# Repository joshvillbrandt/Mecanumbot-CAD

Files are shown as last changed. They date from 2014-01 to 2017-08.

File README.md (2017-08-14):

Mecanumbot-CAD
==============

Solidworks files for the Mecanumbot robot.

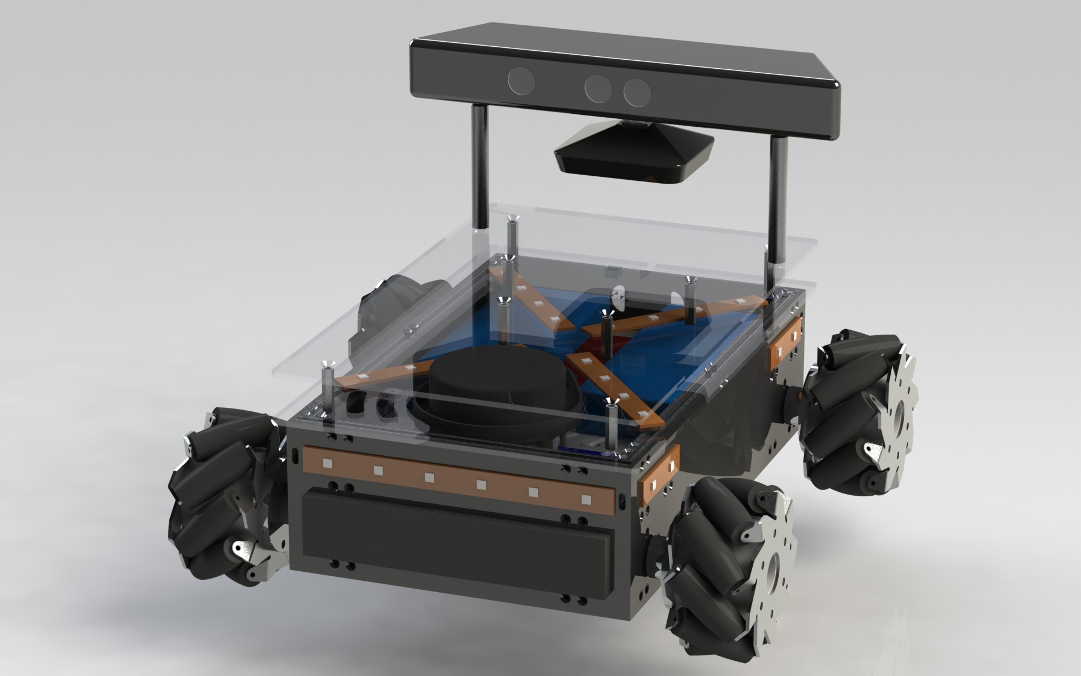
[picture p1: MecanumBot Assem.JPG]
Mecanumbot assembly screenshot


## Todo List

Problems with current design:

* very hard to service
 * too many little screws
 * the robot is very tightly packed
* placing an object on the platform blocks the view of the Kinect
* would ideally like to use a 3D sensor to identify an object on the plaform, but the Kinect's minimum distance is past the front face of the robot, so this doesn't work
* battery plugs are difficult to connect and disconnect
* current battery space was optimized for 4S lipos, but only 3s lipos are being used

Ideas for improvements

* group wires between top and bottom plates into one bundle
* would like to enable automatic charger with a charging dock
* export the model to the ROS urdf to display in rviz

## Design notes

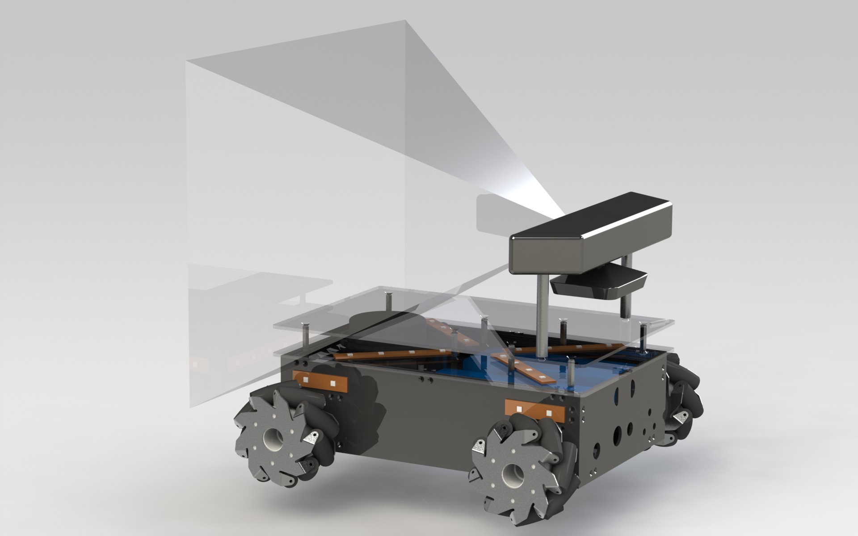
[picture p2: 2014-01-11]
MecanumBot FOV.JPG

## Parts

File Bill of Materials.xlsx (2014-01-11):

Item | Category | Quantity | Vendor | Vendor Part ID | Cost | Sub-Total | Description
12"x24"x1/8" G10/FR4 | Structure | 2 | McMaster | 85345K622 | $34.03 | $68.06
12"x24"x1/8" Polycarbonite | Structure | 3 | McMaster | 8574K41 | $12.52 | $37.56
MicroRax - Small Kit | Structure | 1 | SparkFun | PRT-10809 | $119.95 | $119.95
Devantech MD25 | Drive | 2 | RobotShop | RB-Dev-31 | $75.56 | $151.12
Devantech EMG30 | Drive | 4 | RobotShop | RB-Dev-40 | $54.66 | $218.64
Kinect | Sensor | 1 | Newegg | N82E16874103199 | $138.99 | $138.99
120W wide input DC power supply | Electronics | 1 | Mini-ITX.com | pico-PSU-120WI-25V | $55.00 | $55.00 | picoPSU-120 WI 12-25V Wide Input Plug-in DC-DC ATX PSU (192W AC Adapter Compatible)
Rosewill 1.5' USB cable | Electronics | 1 | Newegg | N82E16812119335 | $3.49 | $3.49
Zotac H67ITX-C-E Motherboard | Electronics | 1 | Newegg | N82E16813500064 | $149.99 | $149.99
PNY 8GB Memory | Electronics | 1 | Newegg | N82E16820178333 | $81.99 | $81.99
Intel Core i3-2100T 2.5GHz | Electronics | 1 | Newegg | N82E16819116394 | $134.99 | $134.99
Kingston 64GB SSD | Electronics | 1 | Newegg | N82E16820139949 | $119.99 | $119.99
Arduino Uno | Electronics | 1 | SparkFun | DEV-11224 | $29.95 | $29.95
Front bumper | Structure | 1 | McMaster | 8694K95 | $15.21 | $15.21
Silicone rubber top | Structure | 1 | McMaster | 86915K24 | $24.77 | $24.77
IDEC E-stop button | Electronics | 1 | Automation and Beyond | XA1E-BV3U01K-R | $33.00 | $33.00
PC on/off button | Electronics | 1 | Digi-Key | CKN10010-ND | $12.01 | $12.01
Power switch | Electronics | 1 | SparkFun | COM-11155 | $1.50 | $1.50
Nexus 100mm Mecanum Wheel Set | Drive | 1 | RobotShop | RB-Nex-13 | $251.66 | $251.66
Turnigy Nanotech 3S 8AHr LiPo | Electronics | 2 | Hobby King | Z80003S-30 | $46.55 | $93.10
Pressure, temp sensor | Electronics | 1 | Adafruit | 391 | $19.95 | $19.95
1m RGB LED Light Strip | Electronics | 1 | Adafruit | 306 | $29.95 | $29.95 | BMP085 breakout
Kinect Standoffs | Structure | 1 | iheartengineering | TURTLE-KINECT-STANDOFF-KIT | $14.95 | $14.95
5mm to 6mm shim | Structure | 1 | McMaster | 8751K63 | $1.20 | $1.20 | Self-lubricating Mds-filled Nylon Strip .02" Thick X 1" Wide, Black, 5 Ft. Length
microRax compatible screws | Structure | 2 | McMaster | 91294A125 | $5.00 | $10.00 | Black Alloy Steel Flat-head Socket Cap Screw, Class 10.9, M3 Size, 5mm Length, .50mm Pitch
thumb screws | Structure | 6 | McMaster | 92581A120 | $2.73 | $16.38 | Black-oxide Steel Knurled Head Thumb Screw, With Straight Shoulder, M3 Thread, 6mm Long
laser scanner | Sensor | 1 | Neato | XV-11 | $332.98 | $332.98
Neato Laser USB | Electronics | 1 | n/a | n/a | $50.00 | $50.00
Mecanumbot Power Board | Electronics | 1 | n/a | n/a | $100.00 | $100.00
xbox controller w/ play and charge | Electronics | 1 | Microsoft | B00936K09S | $61.99 | $61.99
xbox360 wireless gaming receiver | Electronics | 1 | Microsoft | B000HZFCT2 | $16.99 | $16.99
battery charger | Electronics | 1 | Hobby King |  | $22.99 | $22.99 | Turnigy Accucel-6 50W 6A Balancer/Charger w/ accessories
 |  |  |  |  |  | $2418.35

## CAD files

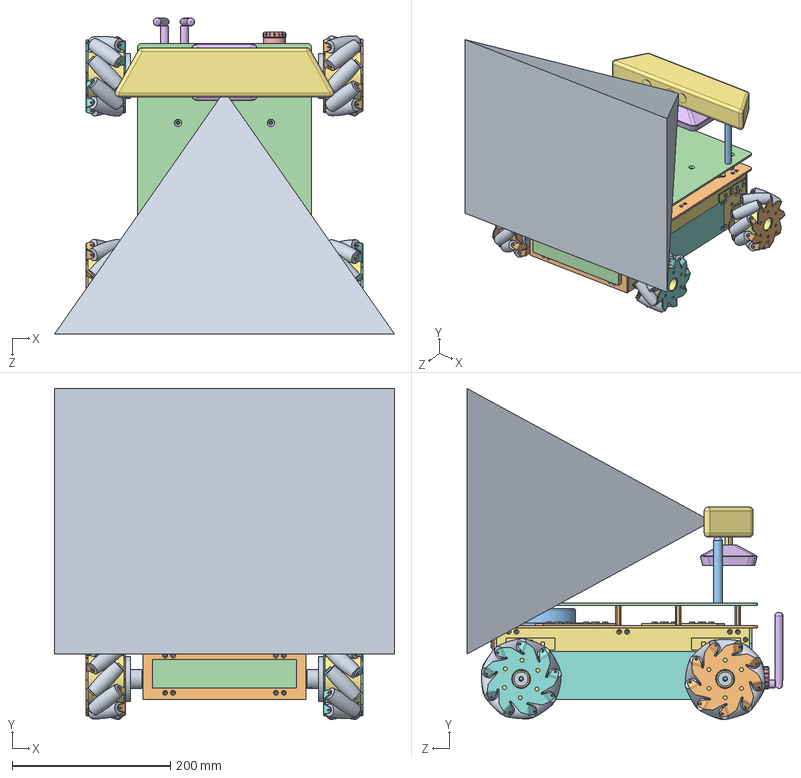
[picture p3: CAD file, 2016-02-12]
MecanumBot Assem.SLDASM
430.0 x 418.8 x 399.7 mm
Body Base Plate
MicroRAX 30cm Beam x 4
MicroRAX 20cm Beam x 4
MicroRAX 6cm Beam x 4
Zotac H67-ITX
Body Mid Plate
Body Side Plate Left
Body Side Cover x 2
Zippy 8Ah 3S1P LiPo x 2
Body Laser Plate
Neato Laser Scanner
Body Top Plate
93657A320 x 4
Kingston SSD
Arduino
Devantech MD25 x 2
MicroRAX 4cm Beam x 2
Body Front Plate
Body Back Plate
Body Back Cover
Body Side Plate Right
Microsoft Kinect Base
Microsoft Kinect Body
Devantech EMG30 x 4
Wheel Hub x 4
Power Board
93657A046 x 4
40mm Fan
93657A035 x 12
Battery Hold x 2
Adafruit 2 RGB LED Strip x 15
93657A003 x 4
95947A059 x 8
Microsoft Kinect Standoff x 2
Bumper
IDEC XA1E-BV3U01K-R
Zotac Antenna x 2
Nexus 100mm Mecanum Wheel Core x 4
Nexus 100mm Mecanum Wheel Left Plate x 4
Nexus 100mm Mecanum Wheel Roller x 36
Nexus 100mm Mecanum Wheel Right Plate x 4

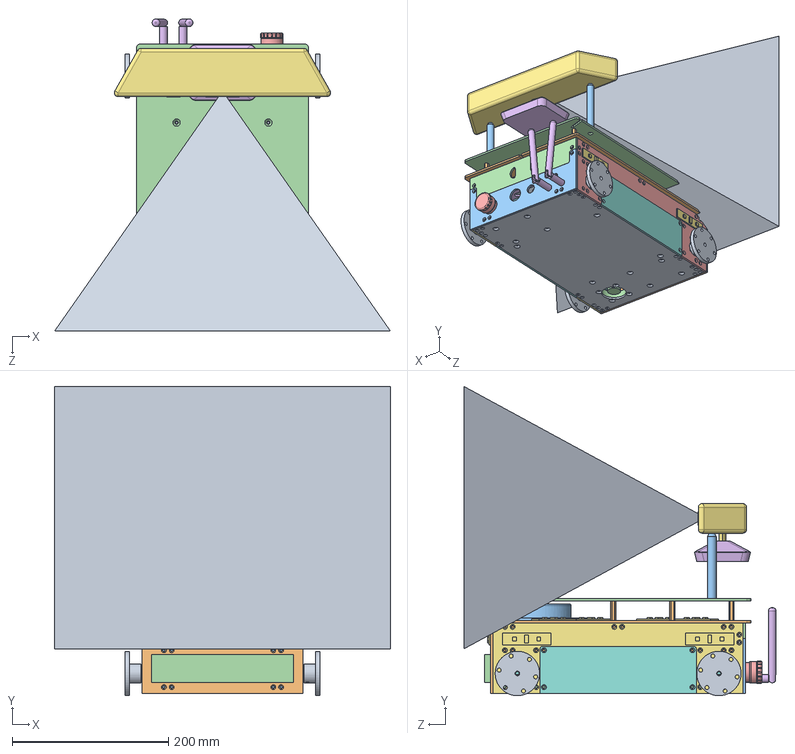
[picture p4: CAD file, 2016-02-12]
Link base_link.SLDASM
430.0 x 395.8 x 399.7 mm
Body Base Plate
MicroRAX 30cm Beam x 4
MicroRAX 20cm Beam x 4
MicroRAX 6cm Beam x 4
Zotac H67-ITX
Body Mid Plate
Body Side Plate Left
Body Side Cover x 2
Zippy 8Ah 3S1P LiPo x 2
Body Laser Plate
Neato Laser Scanner
Body Top Plate
93657A320 x 4
Kingston SSD
Arduino
Devantech MD25 x 2
MicroRAX 4cm Beam x 2
Body Front Plate
Body Back Plate
Body Back Cover
Body Side Plate Right
Microsoft Kinect Base
Microsoft Kinect Body
Devantech EMG30 x 4
Wheel Hub x 4
Power Board
93657A046 x 4
40mm Fan
93657A035 x 12
Battery Hold x 2
Adafruit 2 RGB LED Strip x 15
93657A003 x 4
95947A059 x 8
Microsoft Kinect Standoff x 2
Bumper
IDEC XA1E-BV3U01K-R
Zotac Antenna x 2

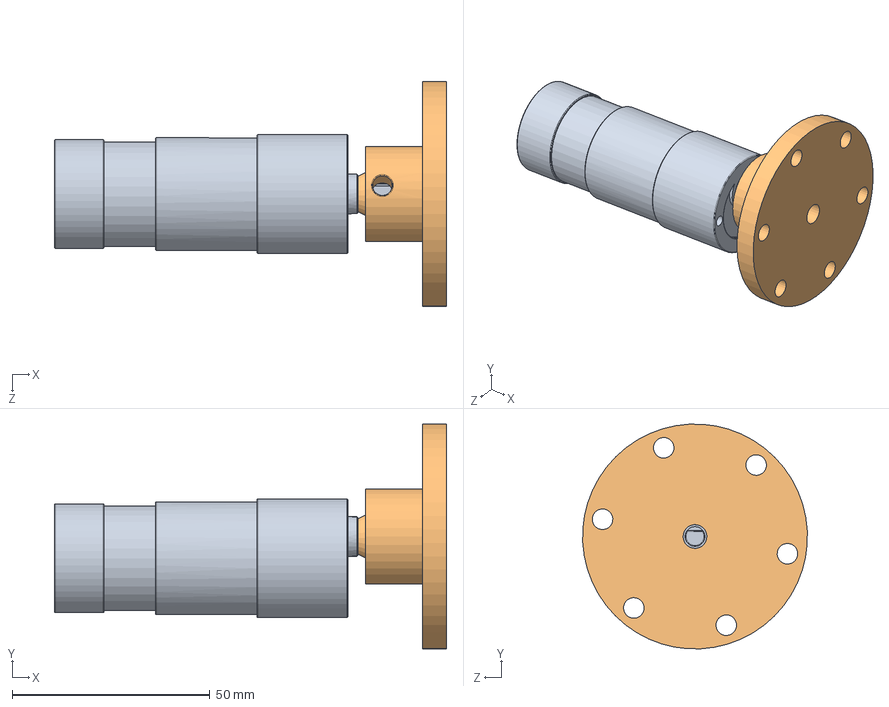
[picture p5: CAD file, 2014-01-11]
Drivetrain Left Assem.SLDASM
99.0 x 56.7 x 56.7 mm
Devantech EMG30
Wheel Hub

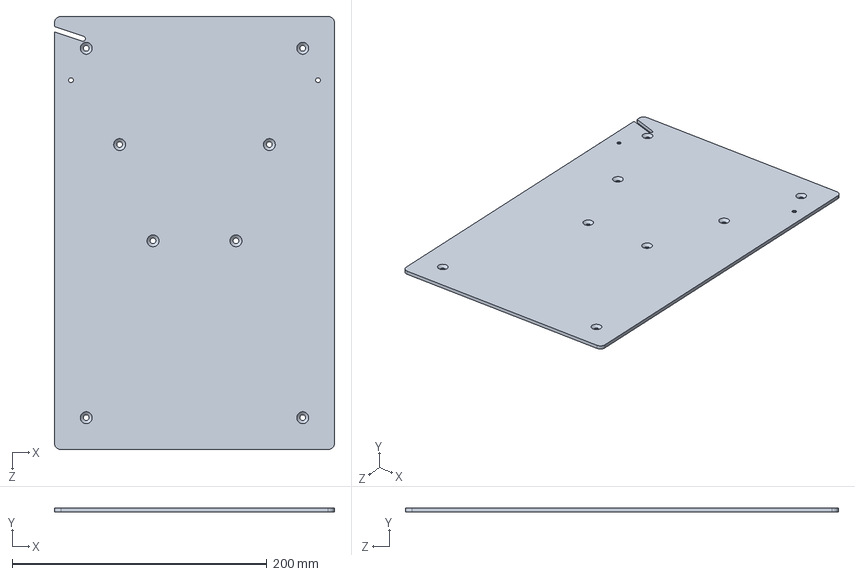
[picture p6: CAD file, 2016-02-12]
Body Top Plate.SLDPRT
220.0 x 3.17 x 340.0 mm

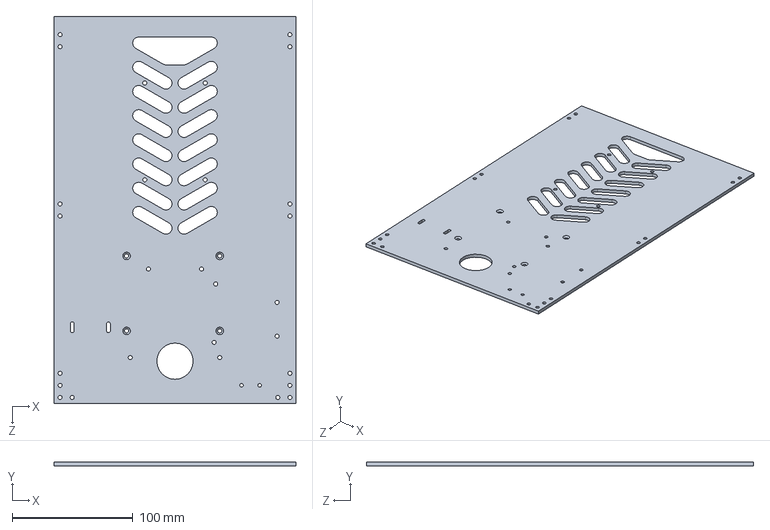
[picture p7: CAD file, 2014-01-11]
Body Mid Plate.SLDPRT
200.0 x 3.17 x 320.0 mm

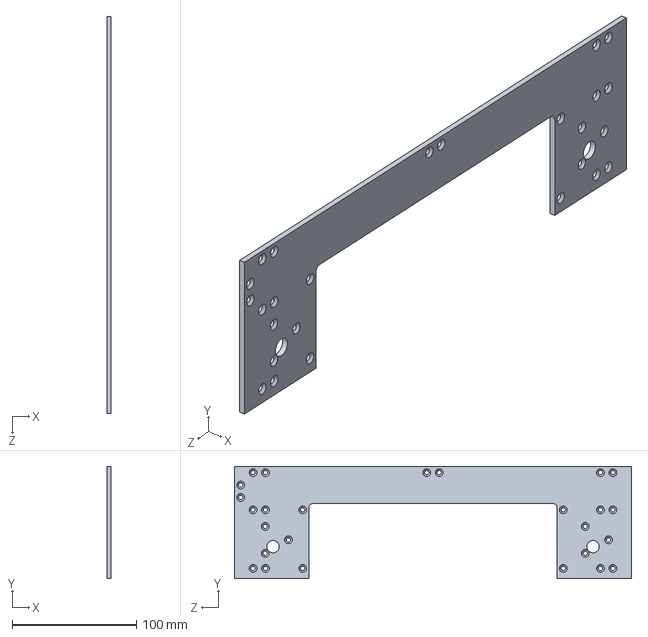
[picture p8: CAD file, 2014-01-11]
Body Side Plate Right.SLDPRT
3.17 x 90.3 x 320.0 mm

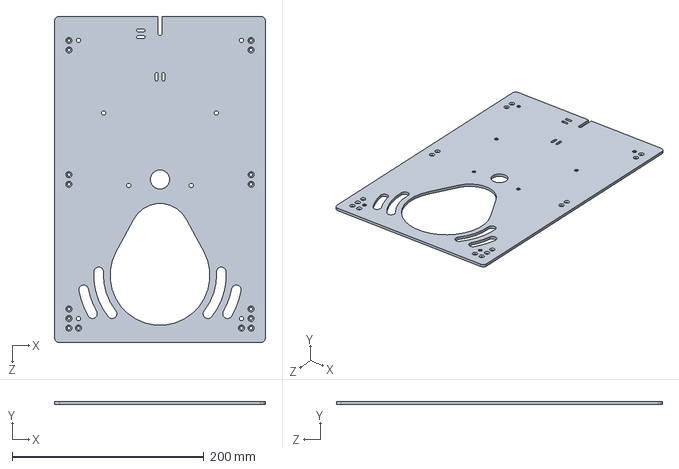
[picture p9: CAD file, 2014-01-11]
Body Laser Plate.SLDPRT
220.0 x 3.17 x 340.0 mm

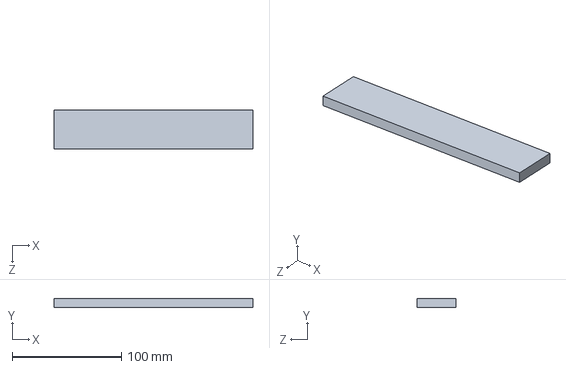
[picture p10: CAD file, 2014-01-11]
Bumper.SLDPRT
182.0 x 8.00 x 36.0 mm

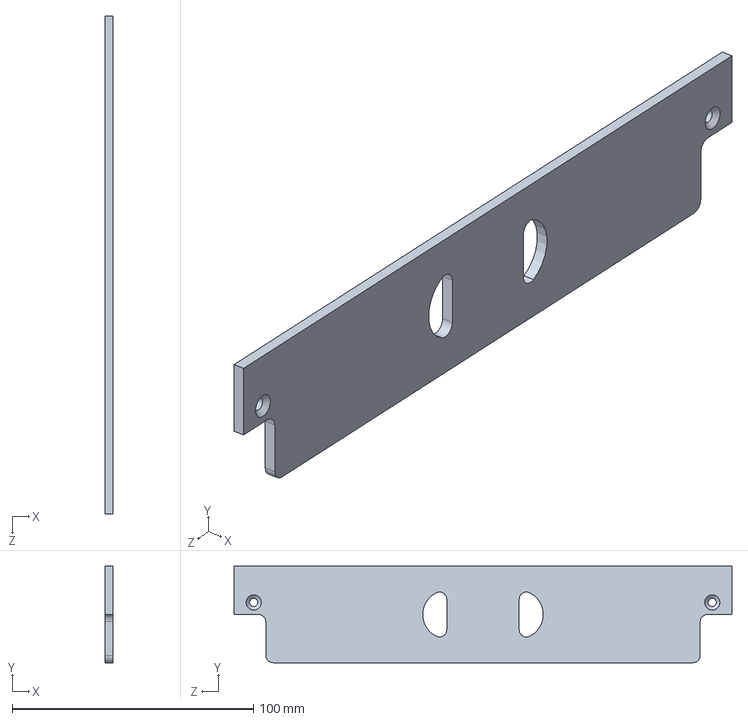
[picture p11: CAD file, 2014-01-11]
Body Back Cover.SLDPRT
3.17 x 40.0 x 206.4 mm

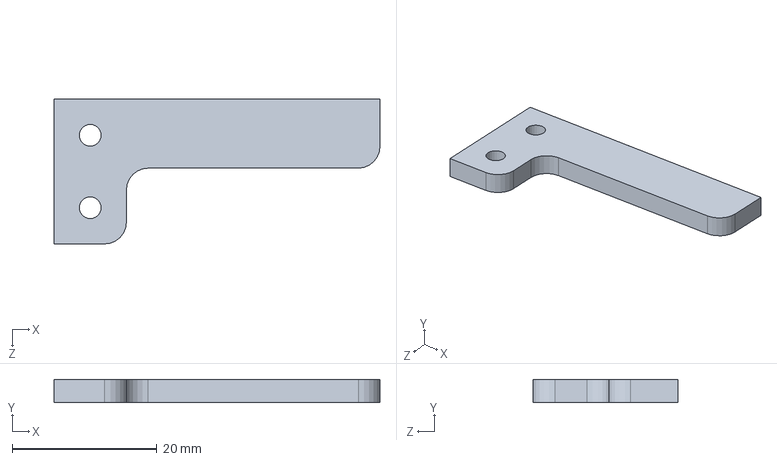
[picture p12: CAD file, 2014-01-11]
Battery Hold.SLDPRT
45.0 x 3.17 x 20.0 mm

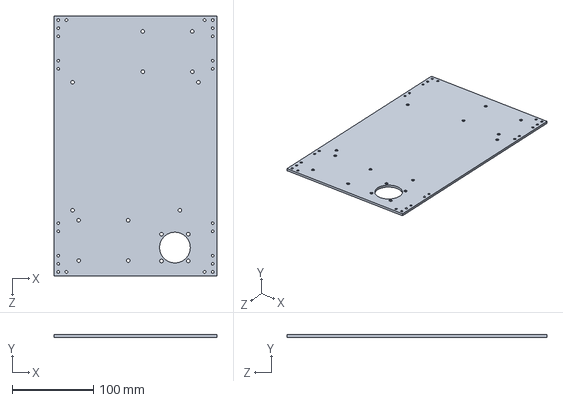
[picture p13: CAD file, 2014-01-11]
Body Base Plate.SLDPRT
200.0 x 3.17 x 320.0 mm

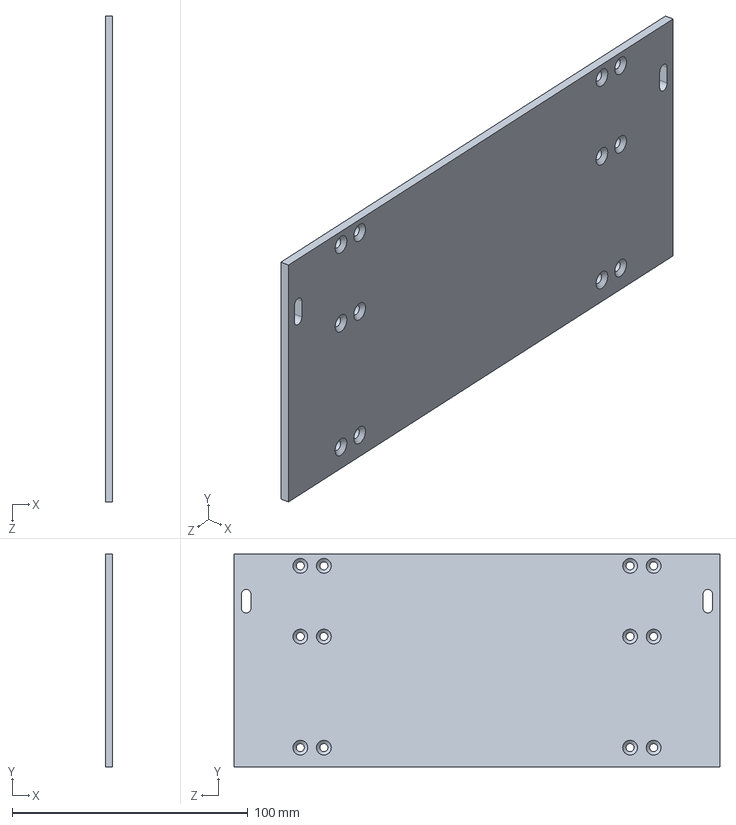
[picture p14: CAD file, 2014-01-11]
Body Front Plate.SLDPRT
3.17 x 90.3 x 206.4 mm

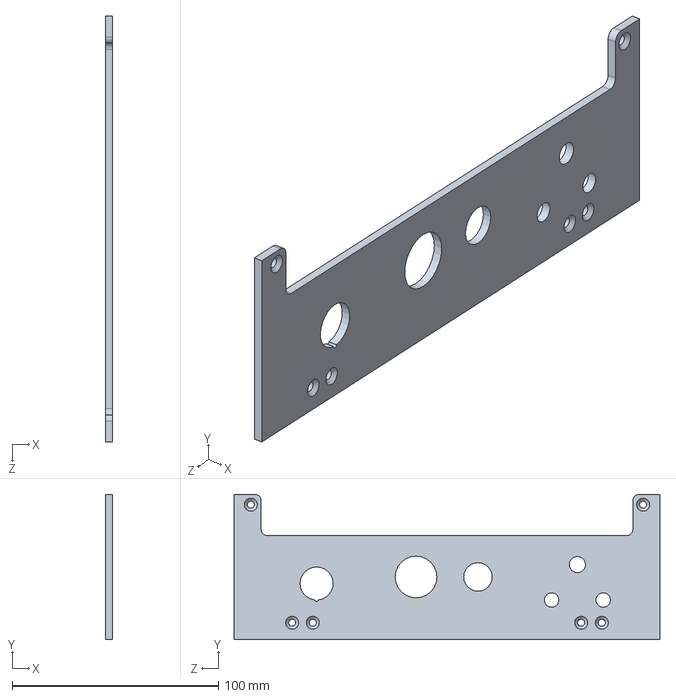
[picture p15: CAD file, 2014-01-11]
Body Back Plate.SLDPRT
3.17 x 70.3 x 206.4 mm

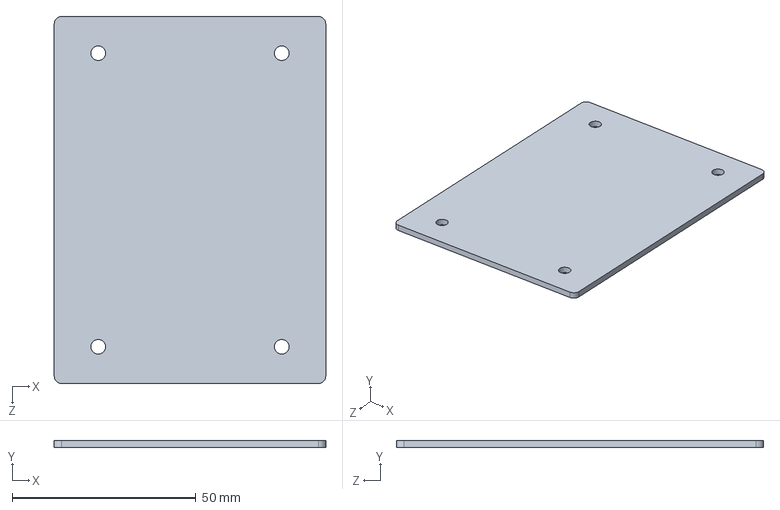
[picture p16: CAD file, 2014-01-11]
Power Board.SLDPRT
74.0 x 2.00 x 100.0 mm

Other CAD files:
Drivetrain Right Assem.SLDASM
Body Side Plate Left.SLDPRT
40mm Fan.SLDPRT
Adafruit 2 RGB LED Strip.SLDPRT
Body Side Cover.SLDPRT
Body Side Plate.SLDPRT

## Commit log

2013-12-19 initial commit from svn
    [40mm Fan.SLDPRT, Adafruit 2 RGB LED Strip.SLDPRT, Battery Hold.SLDPRT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]
2014-01-08 updated BOM
    [Bill of Materials.xlsx]
2014-01-11 completed mecanum wheels
    [Adafruit 2 RGB LED Strip.SLDPRT, MecanumBot Assem.SLDASM]
2014-01-11 adding bumper
    [Bumper.SLDPRT, MecanumBot Assem.SLDASM]
2014-01-11 removing note about modeling mecanum wheels
2014-01-11 better antenna, added e stop, upgraded to solidworks 2012 for urdf exporter
    [40mm Fan.SLDPRT, Adafruit 2 RGB LED Strip.SLDPRT, Battery Hold.SLDPRT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]
2016-02-12 Add embedded URDF export information
    [Body Top Plate.SLDPRT, Link base_link.SLDASM, MecanumBot Assem.SLDASM]
